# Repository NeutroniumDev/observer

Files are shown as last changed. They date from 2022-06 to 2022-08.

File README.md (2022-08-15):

# Observer
Observer is a device that measures the altitude, acceleration, rotation, and location of model rockets. 

As of June 24, 2022, Observer's schematic is complete-ish but untested. It uses the following chips:
- SAMD21G18   (Processing)
- USB-C port (data transfer
  + Protection IC (can be omitted) 
- ISM330         (Rotation and low-acceleration measurements)
- BMP390        (Pressure-based altitude measurements)
- ADXL375          (High-acceleration measurements)
- Micro SD card      (Temporary data storage)
- Ublox MAX M8     (GPS)
  + External LNA
- RFM97C         (LoRa Radio tranceiver)
- PCA9685PW     (LED driver, used as motor driver.)

Future changes (maybe):
-Change the pogo pin pads to headers for easier debugging, and the JTAG pads to
a full JTAG connector.
-Change the logo on the back of the PCB because I won't be using it for the TARC 
competition anymore. 
-Remove the USB-C anti-static protection IC, because it costs money and is most
likely useless.
-Remove a lot of decoupling caps, because I don't really need them
-Find a better way of controlling the servo motors, maybe through connecting them
to GPIO and using a level shifter

**Notes:**

As of June 24th, 2022 the design has not been fully validated. I don't have a 
JTAG debugger and I can't get one right now, so I cant upload a bootloader to upload
code over USB. From what I can tell the voltages look fine and the power management 
works perfectly, but I have not been able to test anything else. Plus, since most of
the schematic is based on reference designs, I see no reason why things *shouldn't*
work. 

To build this for myself I substituted the ISM330 with its non-industrial variant, the
LSM6DSO32. In retrospect I realize that the ISM330 was overkill, and using the LSM6DSO32 
makes the secondary high-g accelerometer redundant in most use cases, since the LSM6 can
already go up to 32G. So, if you're looking to build this for yourself, just get the LSM6
and skip the ADXL375, it will save you ~12 bucks. 

More retrospect: the LNA is probably also not very useful, since when used with
rockets the GPS basically has clear view of the sky with very little blocking the signal, 
apart from maybe the rocket casing, but that's insignificant. If you're building this for yourself, 
you can omit the LNA, but MAKE SURE you change the schematic and board layout so that 
the gps module connects directly to the u.fl connector. The GPS will not work otherwise. 
The LNA also has some really fine pitch pins, so the risk of shorting contacts 
is pretty high. So be careful!

As for the name, 'observer' is staying for now since I can't really think of anything
else. Suggestions would be much appreciated! 

This project is licensed under the GNU General Public License v3.0.
Please use responsibly. You *can* make a missle with this, but that doesn't mean you should.

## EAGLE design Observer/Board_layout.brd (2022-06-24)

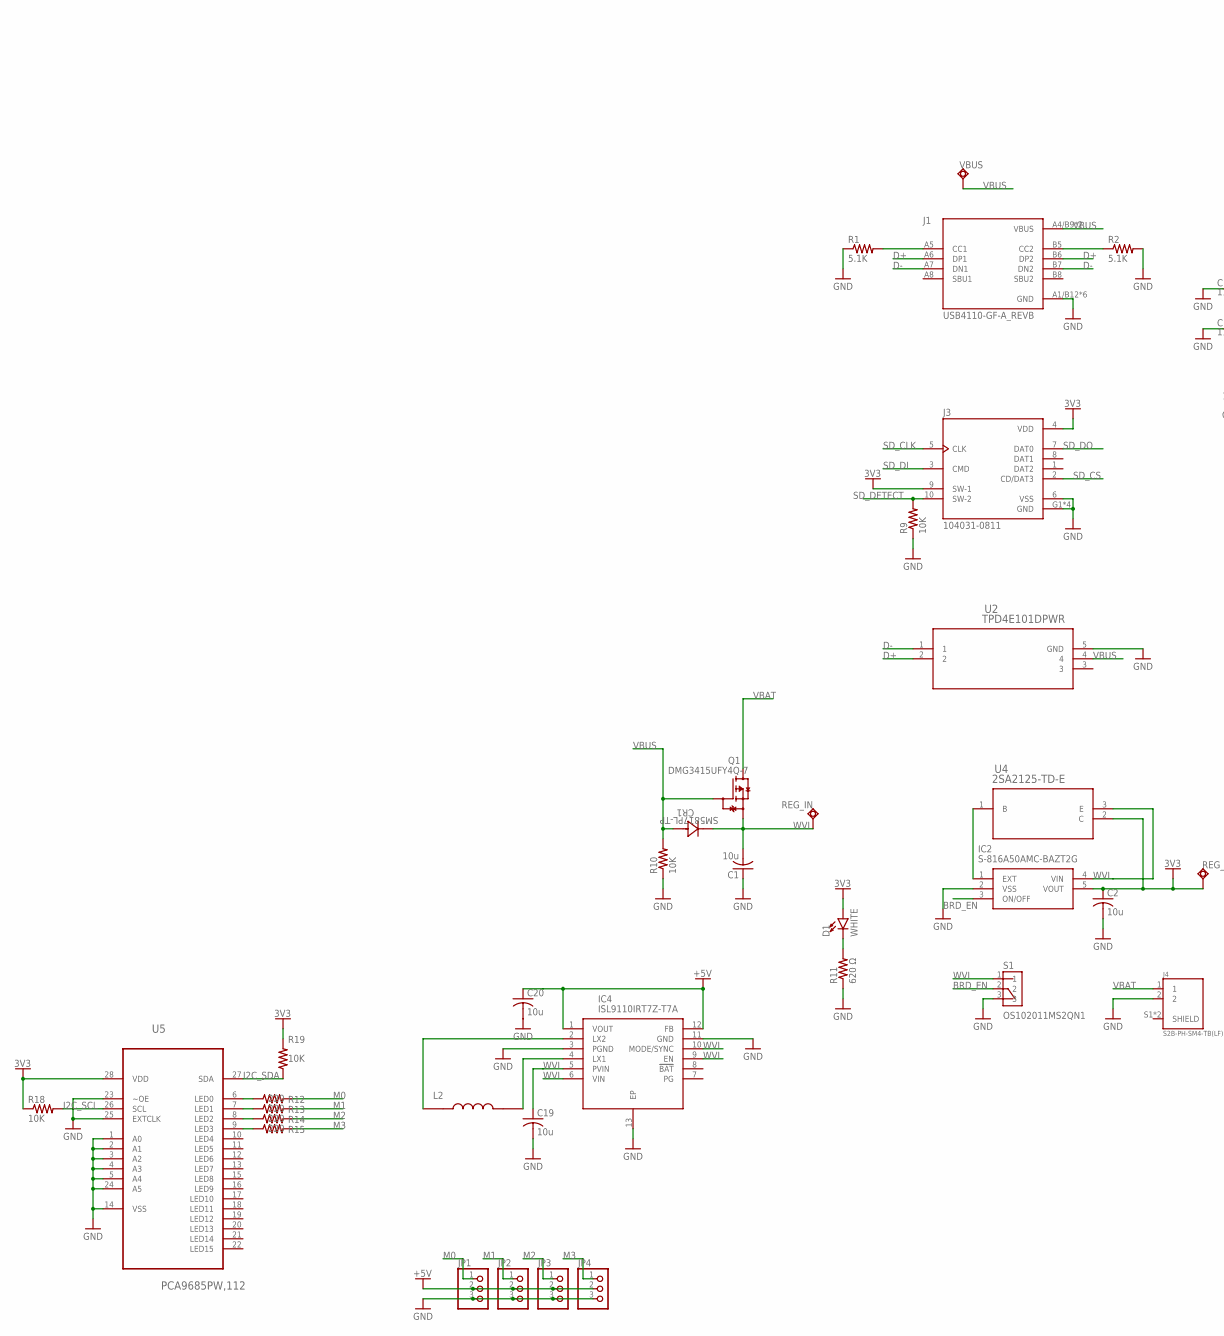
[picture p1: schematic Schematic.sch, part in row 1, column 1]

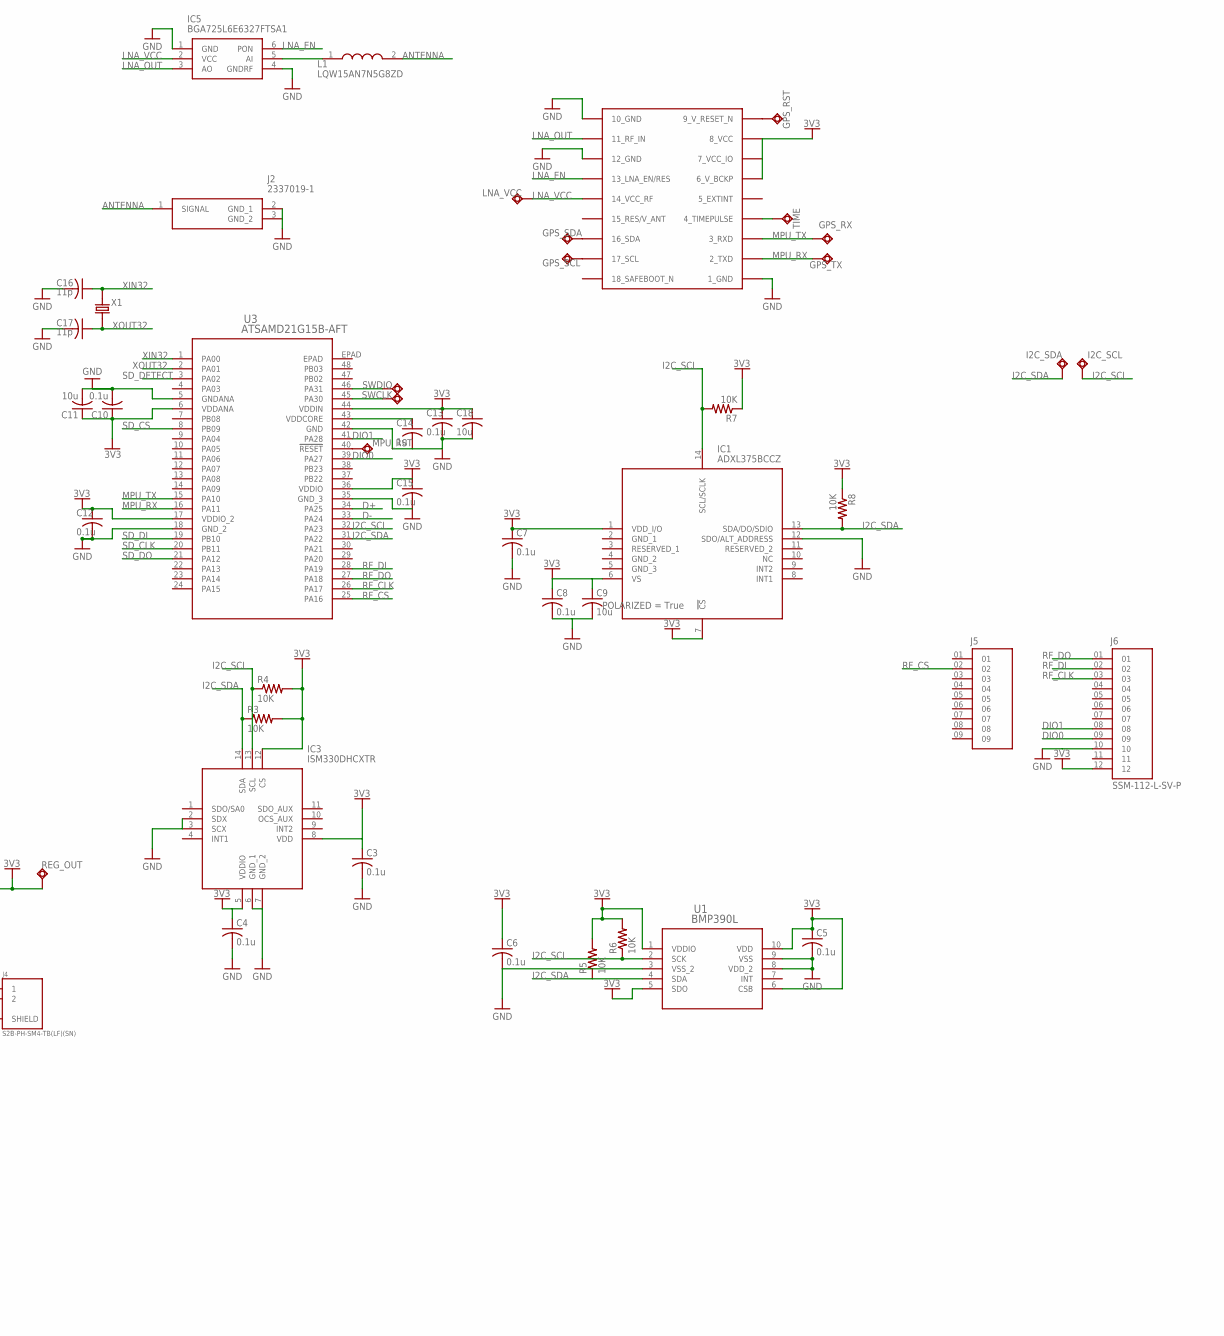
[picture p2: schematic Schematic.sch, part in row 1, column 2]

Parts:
C1, C2, C9, C11: 10u; C0805
C3, C4, C5, C6, C7, C8: 0.1u; C0805
C10, C12, C13, C15: 0.1u; C0603
C14: 1u; C0603
C16, C17: 11p; CAPC1005X60
C18: 10u; C0603
C19, C20: 10u; C0805K
CR1: SM5817PL-TP; CR_5817PL-TP_MCC
D1: WHITE; LED-0603
GPS_RST: TPSQTP20SQ; TP20SQ
GPS_RX: TPSQTP20SQ; TP20SQ
GPS_SCL: TPSQTP20SQ; TP20SQ
GPS_SDA: TPSQTP20SQ; TP20SQ
GPS_TX: TPSQTP20SQ; TP20SQ
I2C_SCL, I2C_SDA: TPSQTP20SQ; TP20SQ
IC1: ADXL375BCCZ; CC-14-1
IC2: S-816A50AMC-BAZT2G; SOT95P275X130-5N
IC3: ISM330DHCXTR; LGA-14(2.5X3X0.86)
IC4: ISL9110IRT7Z-T7A; SON40P300X300X75-13N
IC5: BGA725L6E6327FTSA1; BGS12SN6E6327XTSA1
J1: USB4110-GF-A_REVB; GCT_USB4110-GF-A_REVB
J2: 2337019-1; 23370191
J3: 104031-0811; MOLEX_104031-0811
J4: S2B-PH-SM4-TB(LF)(SN); JST_S2B-PH-SM4-TB(LF)(SN)
J5: SSM-109-L-SV; SAMTEC_SSM-109-L-SV
J6: SSM-112-L-SV-P; SAMTEC_SSM-112-L-SV-P
JP1, JP2, JP3, JP4: PINHD-1X3; 1X03
L1: LQW15AN7N5G8ZD; LQW15CNR20J00B
L2: LQH43PN2R2M26L; IND_LQH43PN2R2M26L
LNA_VCC: TPSQTP20SQ; TP20SQ
MPU_RST: TPSQTP20SQ; TP20SQ
Q1: DMG3415UFY4Q-7; TRANS_DMG3415UFY4Q-7
R1, R2: 5.1K; M0805
R3, R4, R5, R6, R7, R8, R9, R10: 10K; M0805
R11: 620 Ω; R0402
R12, R13, R14, R15: 220; R0805
R18, R19: 10K; R0805
REG_IN: TPSQTP20SQ; TP20SQ
REG_OUT: TPSQTP20SQ; TP20SQ
S1: OS102011MS2QN1; SW_OS102011MS2QN1
SWCLK: TPSQTP20SQ; TP20SQ
SWDIO: TPSQTP20SQ; TP20SQ
TIME: TPSQTP20SQ; TP20SQ
U1: BMP390L; BMP390L_BOS
U2: TPD4E101DPWR; DPW4
U3: ATSAMD21G15B-AFT; TQFP48_7X7MC_MCH
U4: 2SA2125-TD-E; PCP-3_2P5X4P5_ONS
U5: PCA9685PW,112; SOP65P640X110-28N
U$1: MAX-M8
VBUS: TPSQTP20SQ; TP20SQ
X1: ECS-.327-7-34B-TR; XTAL_ECS-.327-7-34B-TR

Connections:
3V3: C2.1, C3.1, C4.1, C5.1, C6.1, C7.1, C8.1, C9.1, C10.1, C11.1, C12.1, C13.1, C15.1, C18.1, D1.A, IC1.1 (VDD_I/O), IC1.6 (VS), IC1.7 (!CS), IC2.5 (VOUT), IC3.5 (VDDIO), IC3.8 (VDD), IC3.12 (CS), J3.4 (VDD), J3.9 (SW-1), J6.12, R3.2, R4.2, R5.2, R6.2, R7.1, R8.1, R18.1, R19.2, REG_OUT.TP, U1.1 (VDDIO), U1.5 (SDO), U1.6 (CSB), U1.10 (VDD), U3.6 (VDDANA), U3.17 (VDDIO_2), U3.36 (VDDIO), U3.44 (VDDIN), U4.2 (C), U5.28 (VDD), U$1.6_V_BCKP, U$1.7_VCC_IO, U$1.8_VCC
+5V: C20.1, IC4.1 (VOUT), IC4.12 (FB), JP1.2, JP2.2, JP3.2, JP4.2
ANTENNA: J2.1 (SIGNAL), L1.2
BRD_EN: IC2.3 (ON/OFF), S1.2
D+: J1.A6 (DP1), J1.B6 (DP2), U2.2, U3.34 (PA25)
D-: J1.A7 (DN1), J1.B7 (DN2), U2.1, U3.33 (PA24)
DIO0: J6.09, U3.39 (PA27)
DIO1: J6.08, U3.41 (PA28)
GND: C1.1, C2.2, C3.2, C4.2, C5.2, C6.2, C7.2, C8.2, C9.2, C10.2, C11.2, C12.2, C13.2, C14.2, C15.2, C16.2, C17.2, C18.2, C19.2, C20.2, IC1.12 (SDO/ALT_ADDRESS), IC2.2 (VSS), IC3.2 (SDX), IC3.3 (SCX), IC3.6 (GND_1), IC3.7 (GND_2), IC4.3 (PGND), IC4.11 (GND), IC4.13 (EP), IC5.1 (GND), IC5.4 (GNDRF), J1.A1/B12 (GND), J1.B1/A12 (GND), J1.S1 (GND), J1.S2 (GND), J1.S3 (GND), J1.S4 (GND), J2.2 (GND_1), J2.3 (GND_2), J3.6 (VSS), J3.G1 (GND), J3.G2 (GND), J3.G3 (GND), J3.G4 (GND), J4.2, J6.10, JP1.3, JP2.3, JP3.3, JP4.3, R1.1, R2.2, R9.1, R10.1, R11.1, S1.3, U1.3 (VSS_2), U1.8 (VDD_2), U1.9 (VSS), U2.5 (GND), U3.5 (GNDANA), U3.18 (GND_2), U3.35 (GND_3), U3.42 (GND), U5.1 (A0), U5.2 (A1), U5.3 (A2), U5.4 (A3), U5.5 (A4), U5.14 (VSS), U5.23 (~OE), U5.24 (A5), U5.25 (EXTCLK), U$1.1_GND, U$1.10_GND, U$1.12_GND
I2C_SCL: I2C_SCL.TP, IC1.14 (SCL/SCLK), IC3.13 (SCL), R4.1, R6.1, R7.2, R18.2, U1.2 (SCK), U3.32 (PA23), U5.26 (SCL)
I2C_SDA: I2C_SDA.TP, IC1.13 (SDA/DO/SDIO), IC3.14 (SDA), R3.1, R5.1, R8.2, R19.1, U1.4 (SDA), U3.31 (PA22), U5.27 (SDA)
LNA_EN: IC5.6 (PON), U$1.13_LNA_EN (13_LNA_EN/RES)
LNA_OUT: IC5.3 (AO), U$1.11_RF_IN
LNA_VCC: IC5.2 (VCC), LNA_VCC.TP, U$1.14_VCC_RF
M0: JP1.1, R12.2
M1: JP2.1, R13.2
M2: JP3.1, R14.2
M3: JP4.1, R15.2
MPU_RX: GPS_TX.TP, U3.16 (PA11), U$1.2_TXD
MPU_TX: GPS_RX.TP, U3.15 (PA10), U$1.3_RXD
unnamed: J1.A5 (CC1), R1.2
unnamed: J1.B5 (CC2), R2.1
unnamed: MPU_RST.TP, U3.40 (!RESET)
unnamed: IC5.5 (AI), L1.1
unnamed: TIME.TP, U$1.4_TIMEPULSE
unnamed: C14.1, U3.43 (VDDCORE)
unnamed: GPS_RST.TP, U$1.9_RESET_N (9_V_RESET_N)
unnamed: IC2.1 (EXT), U4.1 (B)
unnamed: GPS_SDA.TP, U$1.16_SDA
unnamed: GPS_SCL.TP, U$1.17_SCL
unnamed: SWCLK.TP, U3.45 (PA30)
unnamed: SWDIO.TP, U3.46 (PA31)
unnamed: D1.C, R11.2
unnamed: IC4.4 (LX1), L2.2
unnamed: IC4.2 (LX2), L2.1
unnamed: R12.1, U5.6 (LED0)
unnamed: R13.1, U5.7 (LED1)
unnamed: R14.1, U5.8 (LED2)
unnamed: R15.1, U5.9 (LED3)
RF_CLK: J6.03, U3.26 (PA17)
RF_CS: J5.02, U3.25 (PA16)
RF_DI: J6.02, U3.28 (PA19)
RF_DO: J6.01, U3.27 (PA18)
SD_CLK: J3.5 (CLK), U3.20 (PB11)
SD_CS: J3.2 (CD/DAT3), U3.8 (PB09)
SD_DETECT: J3.10 (SW-2), R9.2, U3.3 (PA02)
SD_DI: J3.3 (CMD), U3.19 (PB10)
SD_DO: J3.7 (DAT0), U3.21 (PA12)
VBAT: J4.1, Q1.3 (D)
VBUS: CR1.2, J1.A4/B9 (VBUS), J1.B4/A9 (VBUS), Q1.1 (G), R10.2, U2.4, VBUS.TP
WVI: C1.2, C19.1, CR1.1, IC2.4 (VIN), IC4.5 (PVIN), IC4.6 (VIN), IC4.9 (EN), IC4.10 (MODE/SYNC), Q1.2 (S), REG_IN.TP, S1.1, U4.3 (E)
XIN32: C16.1, U3.1 (PA00), X1.2
XOUT32: C17.1, U3.2 (PA01), X1.1

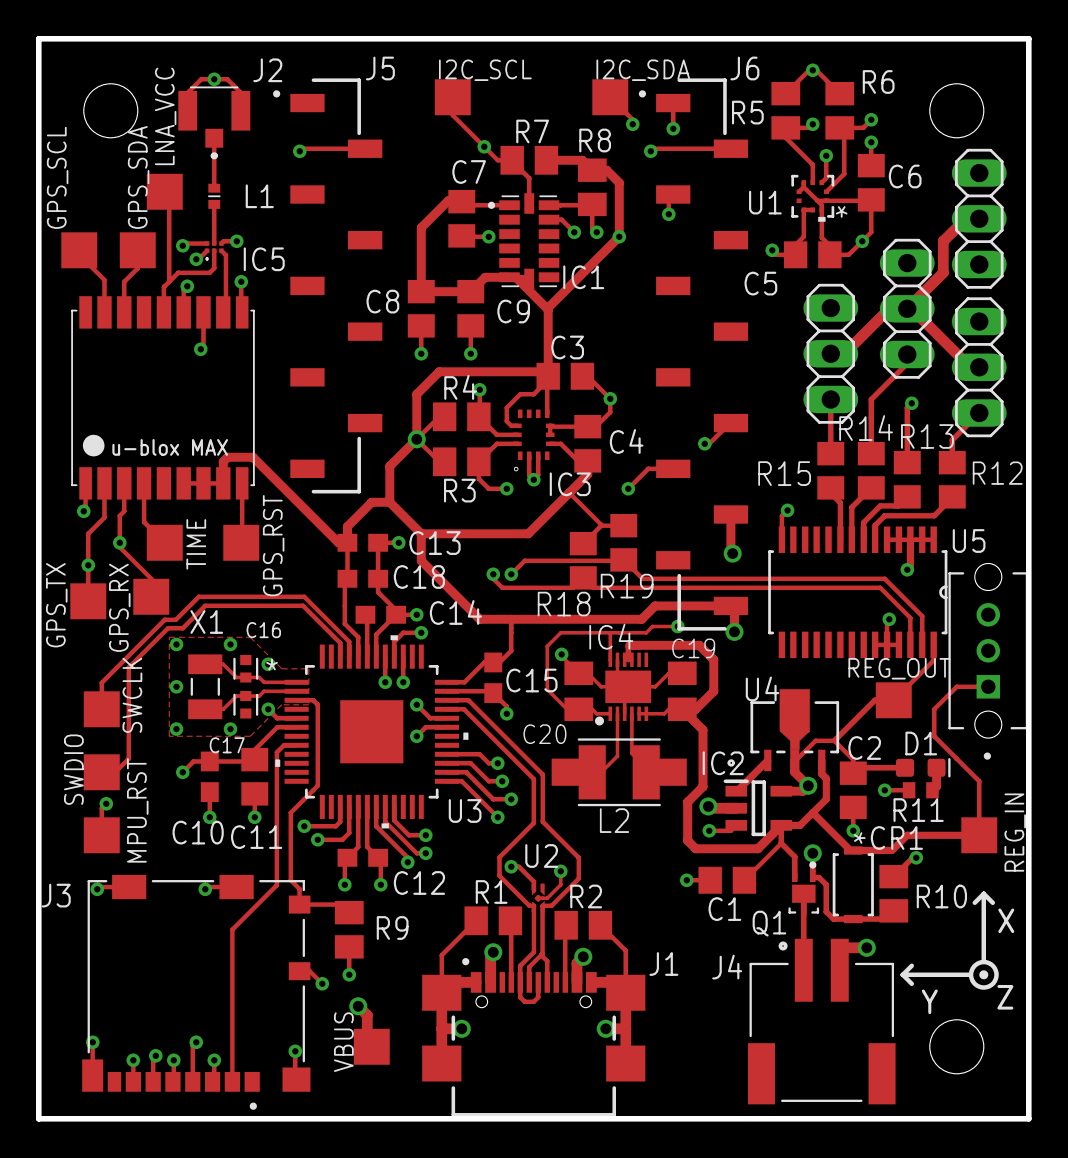
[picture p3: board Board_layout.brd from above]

Board: 4 copper layers, 55.0 x 60.0 mm, 81 parts (0 on the bottom side), 53 nets.

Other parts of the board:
E$1: LOGO

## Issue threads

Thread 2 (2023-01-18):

Accel+Gyro chip (LSM6DS or similar) has a floating address pin and no internal pullup enabled by default

NeutroniumDev, 2023-01-18:
The Accel+Gyro chip has pin 1 (SDO) left floating, which may cause issues. The internal pullup resistor (which would enable switching from address 0x6A to 0x6B) can be enabled in code, but the fix is not ideal. Enabling the pullup resistor requires there to be communication between the MPU and chip, which in testing has been possible using address 0x6B. However, external factors may affect the voltage of this pin enough to cause the address to change. Testing has revealed that something as simple as poking the pin with a needle is enough to cause it to flip. In summary,
The voltage of the address pin is unstable. There is nothing stopping it from choosing one address over the other. It can be stabilized with the help of an internal pullup, but it has to be manually enabled. Manually enabling it becomes difficult, or at least cumbersome, when the chip may be at either address.
The fix is incredibly simple. Connect pin 1 to the adjacent grounded pins.

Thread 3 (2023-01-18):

SD card slot carries risk of short circuit

NeutroniumDev, 2023-01-18:
During testing, a tiny piece of solder got into the SD card slot and shorted the 3V pin to the case, which was grounded. This smoked the power regular transistor, requiring it to be swapped out. In the future, the SD card slot should have protection circuitry and/or a different model of SD card slot to make it less prone to this kind of damage.
Note- when I say SD I mean micro SD.

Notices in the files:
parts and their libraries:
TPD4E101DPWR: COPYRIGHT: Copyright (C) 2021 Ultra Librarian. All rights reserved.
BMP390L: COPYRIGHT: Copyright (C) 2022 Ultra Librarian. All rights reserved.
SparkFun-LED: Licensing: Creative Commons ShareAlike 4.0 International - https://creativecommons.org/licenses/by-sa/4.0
